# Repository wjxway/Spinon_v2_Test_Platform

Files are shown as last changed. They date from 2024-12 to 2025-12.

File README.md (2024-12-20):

# Maneuverable Piccolissimo 4 (MP4) Test Platform Setup Guide

Maneuverable Piccolissimo 4 test platform, or MP4 test platform for short, is a single motor drone system designed to test the dynamics of the drone before we build the full distributed version of MP4 system. Instead of using peer-to-peer communication between drones to achieve control like it will be in the MP4 system, this test platform uses external optical tracking system like Optitrack to obtain high accuracy drone position, making it easier to test subsystems like aerodynamics or control.

For more details of this system, please check (and cite!) our paper at [RSS proceedings website](https://www.roboticsproceedings.org/rss20/p102.html). For assembly guide, please visit [this document](https://1drv.ms/w/s!Aq5Al0CEiWQnkfE0qJTTQATZVnzniQ).

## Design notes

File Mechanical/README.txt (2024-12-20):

If you want to change the design or look at it in more detail, go to:
https://a360.co/3BthnFp (for the drone)
https://a360.co/49MFVFP (for the launcher)

These parts need to be printed using properly dried PAHT-CF filament using BambuLab X1C printer. (If the filament is just opened, then its dry. If it has been left out for a while, then it needs to be dried. You can use the printer's dry filament utility to dry the filament.)

To print the chassis and the wings, import the process presets in Bambu Studio by Files -> Import -> Import presets. When printing the chassis, select the preset "Chassis" and when printing the wings, select the preset "Wings".

The launcher parts can be printed however you want (PLA+standard settings would work just fine). Just note that Launcher_soft need to be printed using TPU.

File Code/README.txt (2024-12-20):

To use the code, install Platform IO on VSCode, then install the ESP32-Arduino dependencies. For guide, please refer to https://www.youtube.com/watch?v=5edPOlQQKmo.

Before using the code, please change the MAC address specifications in FlightTestOptitrack_Drone, FlightTestOptitrack_Syncer and Launcher_new.
There's a small piece of code there that you can uncomment and then read out the MAC address of the devices through serial port.

If you are using a different tracking system other than Optitrack, you only need to modify FlightTestOptitrack_Server.
If your Optitrack system cannot running at 360Hz, contact me or use FlightTestOptitrack_Server\FIRFilterDesign.m in MATLAB to design a new filter compatible with your setup.

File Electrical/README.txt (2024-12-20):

CAM_Files.zip contains the CAM files needed to manufacture and assemble the PCB.

In the schematics, I'm using pinhead as power plugs and SSM6K504NU FET instead of the G2014.
When building the board, make sure you do not install the pinhead (use wires with headers instead) and install Goford G2014 FET.

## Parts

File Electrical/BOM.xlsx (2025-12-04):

Qty | Value | Device | Package | Parts | Description | ARROW_PART_NUMBER | ARROW_PRICE-STOCK | COPYRIGHT | DESCRIPTION.1 | HEIGHT | MANUFACTURER_NAME | MANUFACTURER_PART_NUMBER | MFR_NAME | MOUSER_PART_NUMBER | MOUSER_PRICE-STOCK | MOUSER_TESTING_PART_NUMBER | MOUSER_TESTING_PRICE-STOCK | POPULARITY | REFDES | SPICEPREFIX | TYPE | Column1
2 |  | PINHD-1X2 | 1X02 | JP2, JP3 | PIN HEADER |  |  |  |  |  |  |  |  |  |  |  |  | 98
2 | 0.1uF | C0402_STANDARD | C0402_STANDARD | C4, C18
2 | 1.5K | R0402_STANDARD | R0402_STANDARD | R7, R20
13 | 10K | R0402_STANDARD | R0402_STANDARD | R4, R16, R17, R18, R22, R24, R25, R26, R27, R28, R29, R42, R43
6 | 10R | R0402_STANDARD | R0402_STANDARD | R10, R11, R12, R13, R14, R15
3 | 10uF | C0402_STANDARD | C0402_STANDARD | C14, C15, C16
1 | 150060RS75000 | 150060RS75000 | LEDC1608X80N | LED1 | WURTH ELEKTRONIK - 150060RS75000 - LED, 0603, RED, 250MCD, 625NM |  |  |  | WURTH ELEKTRONIK - 150060RS75000 - LED, 0603, RED, 250MCD, 625NM | 0.8mm | Wurth Elektronik | 150060RS75000 |  | 710-150060RS75000 | https://www.mouser.co.uk/ProductDetail/Wurth-Elektronik/150060RS75000?qs=LlUlMxKIyB3QnmZ3fw%2FVCA%3D%3D
1 | 15K | R0402_STANDARD | R0402_STANDARD | R3
2 | 1K | R0402_STANDARD | R0402_STANDARD | R19, R23
5 | 2.2uF | C0402_STANDARD | C0402_STANDARD | C10, C11, C12, C13, C31
1 | 2.2uF, 16V | C0402_STANDARD | C0402_STANDARD | C17
1 | 22pF | C0402_STANDARD | C0402_STANDARD | C2
1 | 22uF | C-EUC0603 | C0603 | C3 | CAPACITOR, European symbol |  |  |  |  |  |  |  |  |  |  |  |  | 73 |  | C
1 | 2M | R0402_STANDARD | R0402_STANDARD | R1
1 | 3K | R0402_STANDARD | R0402_STANDARD | R33
3 | 4.7K | R0402_STANDARD | R0402_STANDARD | R30, R31, R32
1 | 4.7uF, 16V | C-EUC0603 | C0603 | C1 | CAPACITOR, European symbol |  |  |  |  |  |  |  |  |  |  |  |  | 73 |  | C
8 | 4.7uF, 16V | C-EUC0805 | C0805 | C19, C20, C22, C23, C24, C25, C26, C27 | CAPACITOR, European symbol |  |  |  |  |  |  |  |  |  |  |  |  | 88 |  | C
2 | 5.1K | R0402_STANDARD | R0402_STANDARD | R5, R6
1 | 5mR | R-EU_R0805 | R0805 | R41 | RESISTOR, European symbol |  |  |  |  |  |  |  |  |  |  |  |  | 86 |  | R
1 | 68K | R0402_STANDARD | R0402_STANDARD | R2
1 | 820R | R0402_STANDARD | R0402_STANDARD | R21
1 | AMCA31-2R450G-S1F-T3 | AMCA31-2R450G-S1F-T3 | ANTC3216X140N | ANT1 | ABRACON - AMCA31-2R450G-S1F-T3 - ANTENNA, CHIP, 2.45GHZ, 50 OHM, 1206 | AMCA31-2R450G-S1F-T3 | https://www.arrow.com/en/products/amca31-2r450g-s1f-t3/abracon?region=nac |  | ABRACON - AMCA31-2R450G-S1F-T3 - ANTENNA, CHIP, 2.45GHZ, 50 OHM, 1206 | 1.4mm | ABRACON | AMCA31-2R450G-S1F-T3 |  | 815-CA312R450GS1FT3 | https://www.mouser.co.uk/ProductDetail/ABRACON/AMCA31-2R450G-S1F-T3?qs=AAveGqk956GLuOddQEK40Q%3D%3D
2 | B3U-1000P | B3U-1000P | B3U-1000P | BOOT, RST | OMRON ELECTRONIC COMPONENTS - B3U-1000P - SWITCH, SPST-NO, 0.05A, 12V, SMD | B3U-1000P | https://www.arrow.com/en/products/b3u1000p/omron?region=europe |  | OMRON ELECTRONIC COMPONENTS - B3U-1000P - SWITCH, SPST-NO, 0.05A, 12V, SMD | mm | Omron Electronics | B3U-1000P |  | 653-B3U-1000P | https://www.mouser.co.uk/ProductDetail/Omron-Electronics/B3U-1000P?qs=AO7BQMcsEu4ip80xyf2FwA%3D%3D
1 | EFM8BB21F16G-C-QFN20R | EFM8BB21F16G-C-QFN20R | EFM8BB21F16GCQFN20R | IC1 | SILICON LABS - EFM8BB21F16G-C-QFN20R - 8 Bit MCU, EFM8 Family EFM8BB Series Microcontrollers, 50 MHz, 16 KB, 2.25 KB, 20 Pins, QFN | EFM8BB21F16G-C-QFN20R | https://www.arrow.com/en/products/efm8bb21f16g-c-qfn20r/silicon-labs?region=nac |  | SILICON LABS - EFM8BB21F16G-C-QFN20R - 8 Bit MCU, EFM8 Family EFM8BB Series Microcontrollers, 50 MHz, 16 KB, 2.25 KB, 20 Pins, QFN | 0.8mm | Silicon Labs | EFM8BB21F16G-C-QFN20R |  | 634-8BB21F16GCQFN20R | https://www.mouser.co.uk/ProductDetail/Silicon-Labs/EFM8BB21F16G-C-QFN20R?qs=6viq6gG%252BWEv0H4U5d9AR5A%3D%3D
1 | ESP32-S3-PICO-1-N8R2 | ESP32-S3-PICO-1-N8R2 | QFN56_7X7_EXP | U2 |  |  |  | Copyright (C) 2024 Ultra Librarian. All rights reserved. |  |  |  | ESP32-S3-PICO-1-N8R2 | Espressif Systems
1 | FD6288Q | FD6288Q | QFN50P400X400X90-25N | IC2 | QFN-24 MOS Drivers RoHS |  |  |  | QFN-24 MOS Drivers RoHS | 0.9mm | Fortior Tech | FD6288Q
1 | GSB1C41110SSHR | GSB1C41110SSHR | GSB1C41110SSHR | J1 | USB2.0, Type C, Top mount, Center Height 1.63mm, Single Row Surface Mount |  |  |  | USB2.0, Type C, Top mount, Center Height 1.63mm, Single Row Surface Mount | 3.41mm | Amphenol Communications Solutions | GSB1C41110SSHR
4 | IN4148WT | IN4148WT | SODFL1608X70N | D1, D2, D3, D4 | SMD Small Signal Switching Diode |  |  |  | SMD Small Signal Switching Diode | 0.7mm | Diotec | IN4148WT
1 | INA231AIYFFR | INA231AIYFFR | BGA12C40P3X4_139X164X62 | IC9 | 28V, Bi-Directional, Low-/High-Side, I2C Out Current/Power Monitor w/Alert in WCSP | INA231AIYFFR | https://www.arrow.com/en/products/ina231aiyffr/texas-instruments?utm_currency=USD&region=nac |  | 28V, Bi-Directional, Low-/High-Side, I2C Out Current/Power Monitor w/Alert in WCSP | 0.625mm | Texas Instruments | INA231AIYFFR |  | 595-INA231AIYFFR | https://www.mouser.co.uk/ProductDetail/Texas-Instruments/INA231AIYFFR?qs=s44pgLhgXQjbCj637LJKHw%3D%3D
1 | SM0605RGB | SM0605RGB | SM0605RGB | LED3 | SM0605RGB, Bivar 470 nm, 525 nm, 635 nm 3 RGB LED, 4-Pin 0605 Clear SMD package | SM0605RGB | https://www.arrow.com/en/products/sm0605rgb/bivar?region=nac |  | SM0605RGB, Bivar 470 nm, 525 nm, 635 nm 3 RGB LED, 4-Pin 0605 Clear SMD package | 0.6mm | Bivar | SM0605RGB |  | 749-SM0605TCRGB | https://www.mouser.co.uk/ProductDetail/Bivar/SM0605RGB?qs=pfd5qewlna4PrJ6da7Zedg%3D%3D
6 | Goford G2014 | Goford G2014 | Goford G2014 | Q6, Q7, Q8, Q9, Q10, Q11 | Small Low ON resistance MOSFETs |  |  |  | Small Low ON resistance MOSFETs | 0.8mm | Toshiba | SSM6K504NU |  | N/A | https://www.mouser.co.uk/ProductDetail/Toshiba/SSM6K504NU?qs=TCEIJQ6oZHxcnwqdmxHSFw%3D%3D
1 | TPSM863252RDXR | TPSM863252RDXR | RDX0007A-MFG | U1 |  |  |  | Copyright (C) 2024 Ultra Librarian. All rights reserved. |  |  |  | TPSM863252RDXR | Texas Instruments |  |  |  |  |  | RefDes |  | TYPE

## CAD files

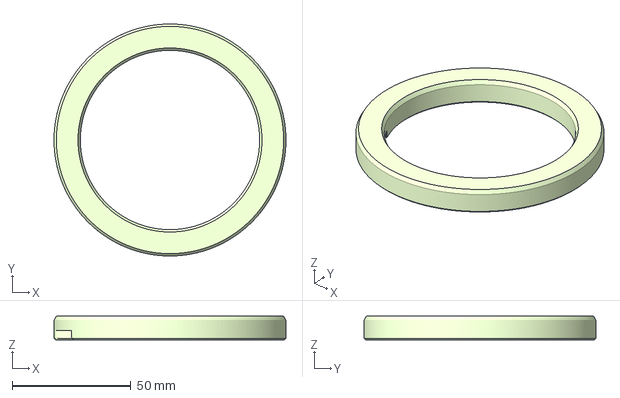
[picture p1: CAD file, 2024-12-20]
Mechanical/Launcher_soft.3mf
97.6 x 97.6 x 10.0 mm

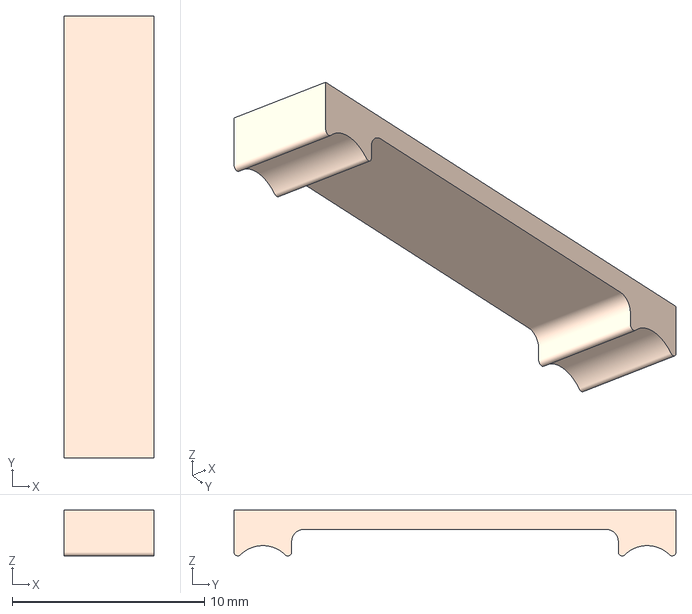
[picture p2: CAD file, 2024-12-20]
Mechanical/Launcher_cap_1.3mf
4.70 x 23.0 x 2.38 mm

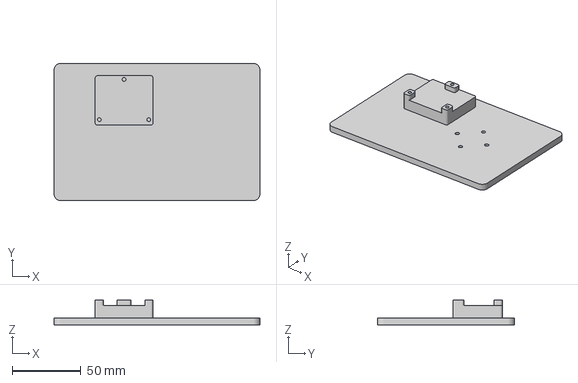
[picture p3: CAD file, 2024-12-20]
Mechanical/Launcher_base.3mf
150.0 x 100.0 x 18.1 mm

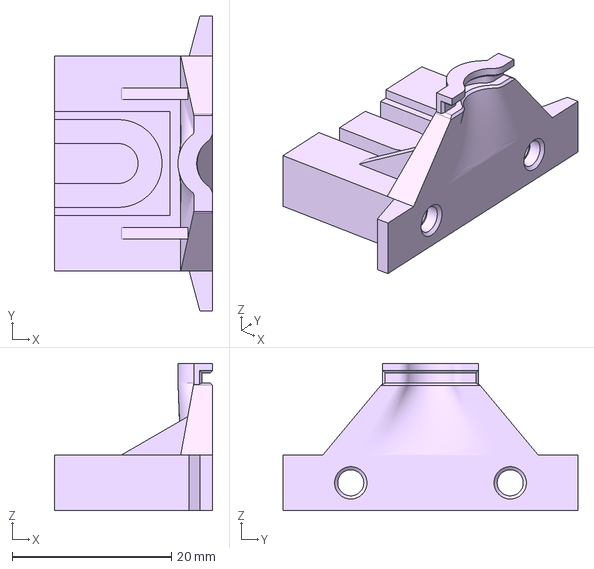
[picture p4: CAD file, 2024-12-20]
Mechanical/Launcher_slider.3mf
19.9 x 37.0 x 18.5 mm

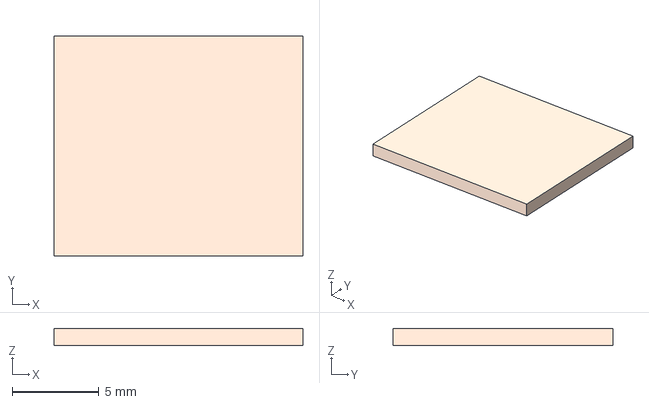
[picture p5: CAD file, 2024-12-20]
Mechanical/Launcher_cap_2.3mf
14.3 x 12.7 x 1.00 mm

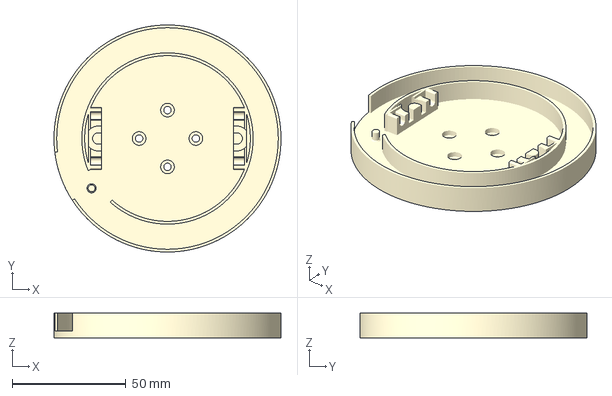
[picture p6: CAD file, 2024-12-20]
Mechanical/Launcher_platform.3mf
100.0 x 100.0 x 11.0 mm

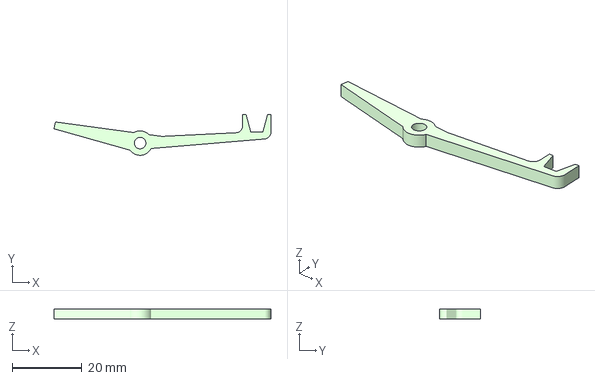
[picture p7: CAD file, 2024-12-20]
Mechanical/Launcher_lever.3mf
62.2 x 11.6 x 3.00 mm

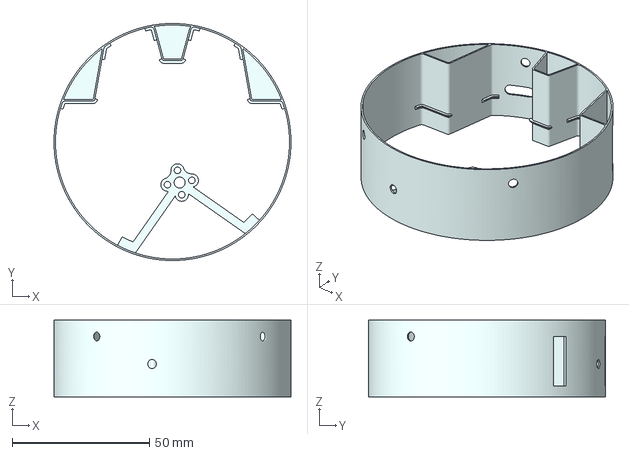
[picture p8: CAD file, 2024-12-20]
Mechanical/Chassis.3mf
86.3 x 86.3 x 28.0 mm

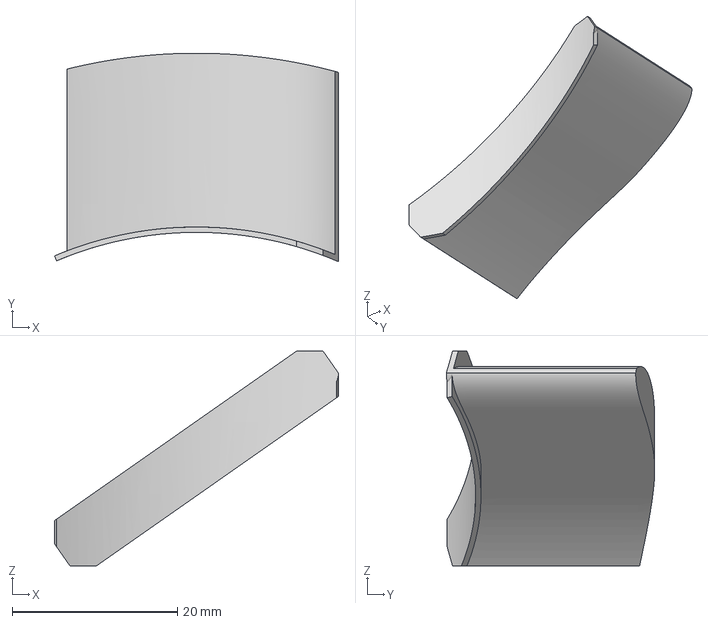
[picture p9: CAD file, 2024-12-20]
Mechanical/Wings.3mf
34.4 x 25.2 x 26.0 mm

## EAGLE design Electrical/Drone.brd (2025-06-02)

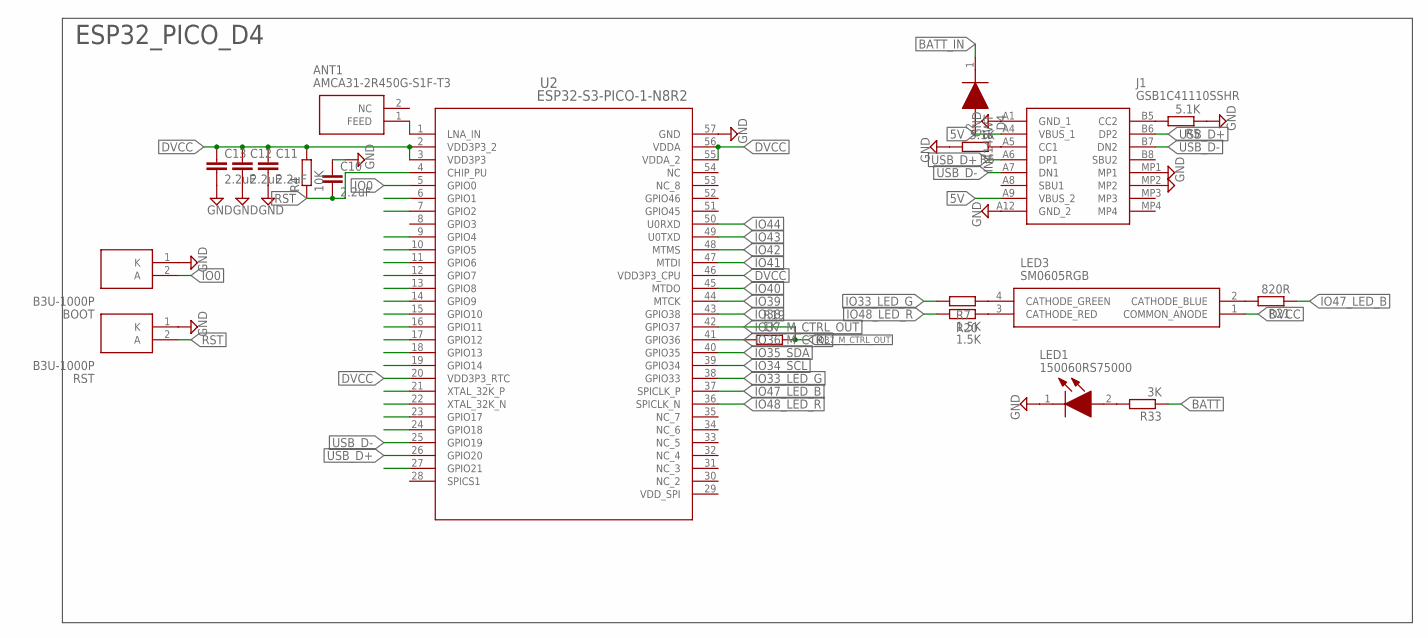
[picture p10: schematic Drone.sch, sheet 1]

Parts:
ANT1: AMCA31-2R450G-S1F-T3; ANTC3216X140N
BOOT: B3U-1000P
C10, C11, C12, C13: 2.2uF; C0402_STANDARD
D4: IN4148WT; SODFL1608X70N
J1: GSB1C41110SSHR
LED1: 150060RS75000; LEDC1608X80N
LED3: SM0605RGB
R4: 10K; R0402_STANDARD
R5, R6: 5.1K; R0402_STANDARD
R7, R20: 1.5K; R0402_STANDARD
R19: 1K; R0402_STANDARD
R21: 820R; R0402_STANDARD
R33: 3K; R0402_STANDARD
RST: B3U-1000P
U2: ESP32-S3-PICO-1-N8R2; QFN56_7X7_EXP

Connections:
5V: D4.2 (A), J1.A4 (VBUS_1), J1.A9 (VBUS_2)
BATT: R33.1; also elsewhere on the board
BATT_IN: D4.1 (K); also elsewhere on the board
DVCC: C11.1, C12.1, C13.1, LED3.1 (COMMON_ANODE), R4.2, U2.2 (VDD3P3_2), U2.3 (VDD3P3), U2.20 (VDD3P3_RTC), U2.46 (VDD3P3_CPU), U2.55 (VDDA_2), U2.56 (VDDA); also elsewhere on the board
GND: BOOT.1 (K), C10.1, C11.2, C12.2, C13.2, J1.A1 (GND_1), J1.A12 (GND_2), J1.MP1, J1.MP2, LED1.1 (K), R5.1, R6.2, RST.1 (K), U2.57 (GND); also elsewhere on the board
IO0: BOOT.2 (A), U2.5 (GPIO0)
IO33_LED_G: R7.2, U2.38 (GPIO33)
IO34_SCL: U2.39 (GPIO34); also elsewhere on the board
IO35_SDA: U2.40 (GPIO35); also elsewhere on the board
IO36_M_CTRL: R19.2, U2.41 (GPIO36)
IO37_M_CTRL_OUT: R19.1, U2.42 (GPIO37); also elsewhere on the board
IO38: U2.43 (GPIO38)
IO39: U2.44 (MTCK)
IO40: U2.45 (MTDO)
IO41: U2.47 (MTDI)
IO42: U2.48 (MTMS)
IO43: U2.49 (U0TXD)
IO44: U2.50 (U0RXD)
IO47_LED_B: R21.1, U2.37 (SPICLK_P)
IO48_LED_R: R20.2, U2.36 (SPICLK_N)
unnamed: ANT1.1 (FEED), U2.1 (LNA_IN)
unnamed: LED3.4 (CATHODE_GREEN), R7.1
unnamed: J1.A5 (CC1), R6.1
unnamed: LED1.2 (A), R33.2
unnamed: LED3.2 (CATHODE_BLUE), R21.2
unnamed: J1.B5 (CC2), R5.2
unnamed: LED3.3 (CATHODE_RED), R20.1
RST: C10.2, R4.1, RST.2 (A), U2.4 (CHIP_PU)
USB_D+: J1.A6 (DP1), J1.B6 (DP2), U2.26 (GPIO20)
USB_D-: J1.A7 (DN1), J1.B7 (DN2), U2.25 (GPIO19)
VDD_SPI: U2.29 (VDD_SPI)

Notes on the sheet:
ESP32_PICO_D4

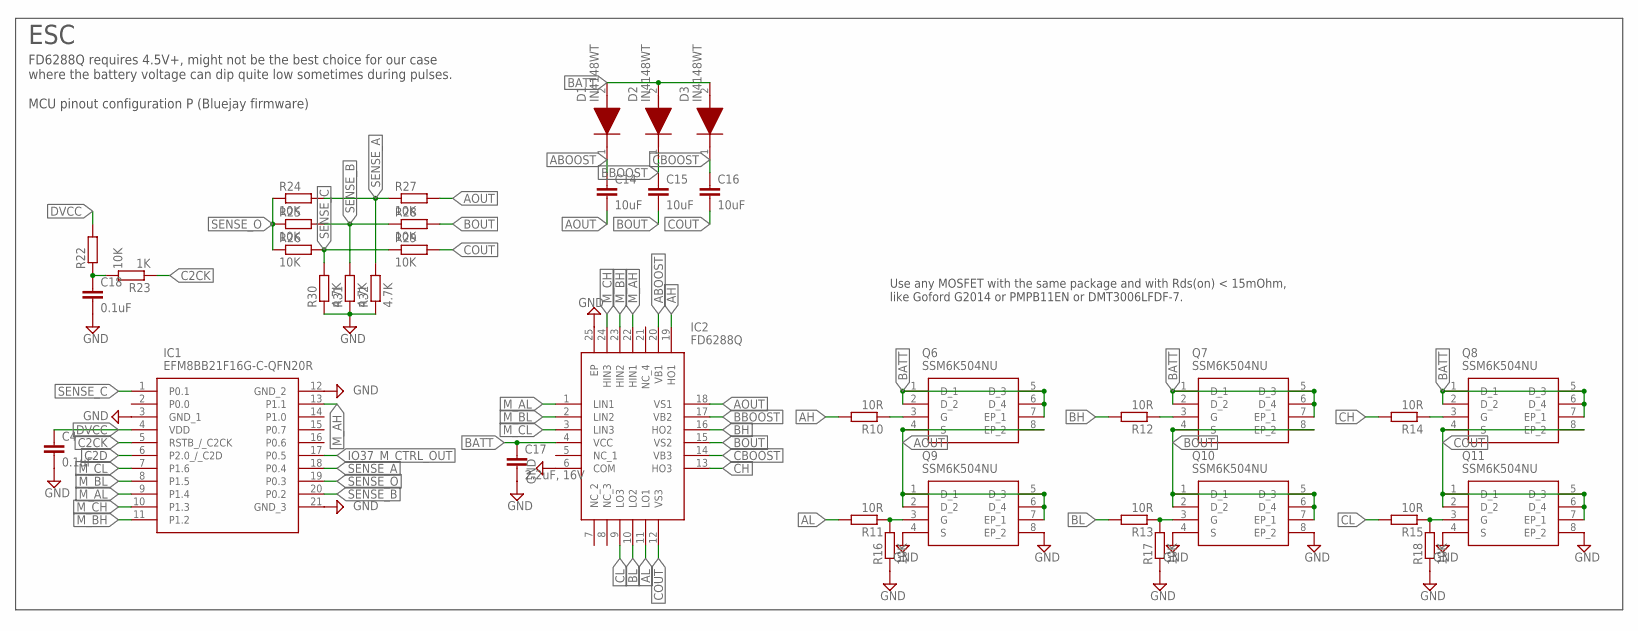
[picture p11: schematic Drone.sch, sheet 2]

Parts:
C4, C18: 0.1uF; C0402_STANDARD
C14, C15, C16: 10uF; C0402_STANDARD
C17: 2.2uF, 16V; C0402_STANDARD
D1, D2, D3: IN4148WT; SODFL1608X70N
IC1: EFM8BB21F16G-C-QFN20R; EFM8BB21F16GCQFN20R
IC2: FD6288Q; QFN50P400X400X90-25N
Q6, Q7, Q8, Q9, Q10, Q11: SSM6K504NU
R10, R11, R12, R13, R14, R15: 10R; R0402_STANDARD
R16, R17, R18, R22, R24, R25, R26, R27, R28, R29: 10K; R0402_STANDARD
R23: 1K; R0402_STANDARD
R30, R31, R32: 4.7K; R0402_STANDARD

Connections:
ABOOST: C14.1, D1.1 (K), IC2.20 (VB1)
AH: IC2.19 (HO1), R10.2
AL: IC2.11 (LO1), R11.2
AOUT: C14.2, IC2.18 (VS1), Q6.4 (S), Q6.8 (EP_2), Q9.1 (D_1), Q9.2 (D_2), Q9.5 (D_3), Q9.6 (D_4), Q9.7 (EP_1), R27.2
BATT: C17.1, D1.2 (A), D2.2 (A), D3.2 (A), IC2.4 (VCC), Q6.1 (D_1), Q6.2 (D_2), Q6.5 (D_3), Q6.6 (D_4), Q6.7 (EP_1), Q7.1 (D_1), Q7.2 (D_2), Q7.5 (D_3), Q7.6 (D_4), Q7.7 (EP_1), Q8.1 (D_1), Q8.2 (D_2), Q8.5 (D_3), Q8.6 (D_4), Q8.7 (EP_1); also elsewhere on the board
BBOOST: C15.1, D2.1 (K), IC2.17 (VB2)
BH: IC2.16 (HO2), R12.2
BL: IC2.10 (LO2), R13.2
BOUT: C15.2, IC2.15 (VS2), Q7.4 (S), Q7.8 (EP_2), Q10.1 (D_1), Q10.2 (D_2), Q10.5 (D_3), Q10.6 (D_4), Q10.7 (EP_1), R28.2
C2CK: IC1.5 (RSTB_/_C2CK), R23.1
C2D: IC1.6 (P2.0_/_C2D)
CBOOST: C16.1, D3.1 (K), IC2.14 (VB3)
CH: IC2.13 (HO3), R14.2
CL: IC2.9 (LO3), R15.2
COUT: C16.2, IC2.12 (VS3), Q8.4 (S), Q8.8 (EP_2), Q11.1 (D_1), Q11.2 (D_2), Q11.5 (D_3), Q11.6 (D_4), Q11.7 (EP_1), R29.2
DVCC: C4.1, IC1.4 (VDD), R22.2; also elsewhere on the board
GND: C4.2, C17.2, C18.2, IC1.3 (GND_1), IC1.12 (GND_2), IC1.21 (GND_3), IC2.6 (COM), IC2.25 (EP), Q9.4 (S), Q9.8 (EP_2), Q10.4 (S), Q10.8 (EP_2), Q11.4 (S), Q11.8 (EP_2), R16.1, R17.1, R18.1, R30.1, R31.1, R32.1; also elsewhere on the board
IO37_M_CTRL_OUT: IC1.17 (P0.5); also elsewhere on the board
M_AH: IC1.13 (P1.1), IC2.22 (HIN1)
M_AL: IC1.9 (P1.4), IC2.1 (LIN1)
M_BH: IC1.11 (P1.2), IC2.23 (HIN2)
M_BL: IC1.8 (P1.5), IC2.2 (LIN2)
M_CH: IC1.10 (P1.3), IC2.24 (HIN3)
M_CL: IC1.7 (P1.6), IC2.3 (LIN3)
unnamed: Q6.3 (G), R10.1
unnamed: Q9.3 (G), R11.1, R16.2
unnamed: Q7.3 (G), R12.1
unnamed: Q10.3 (G), R13.1, R17.2
unnamed: Q8.3 (G), R14.1
unnamed: Q11.3 (G), R15.1, R18.2
unnamed: C18.1, R22.1, R23.2
SENSE_A: IC1.18 (P0.4), R24.2, R27.1, R32.2
SENSE_B: IC1.20 (P0.2), R25.2, R28.1, R31.2
SENSE_C: IC1.1 (P0.1), R26.2, R29.1, R30.2
SENSE_O: IC1.19 (P0.3), R24.1, R25.1, R26.1

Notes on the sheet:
ESC
FD6288Q requires 4.5V+, might not be the best choice for our case where the battery voltage can dip quite low sometimes during pulses. MCU pinout configuration P (Bluejay firmware)
Use any MOSFET with the same package and with Rds(on) < 15mOhm, like Goford G2014 or PMPB11EN or DMT3006LFDF-7.

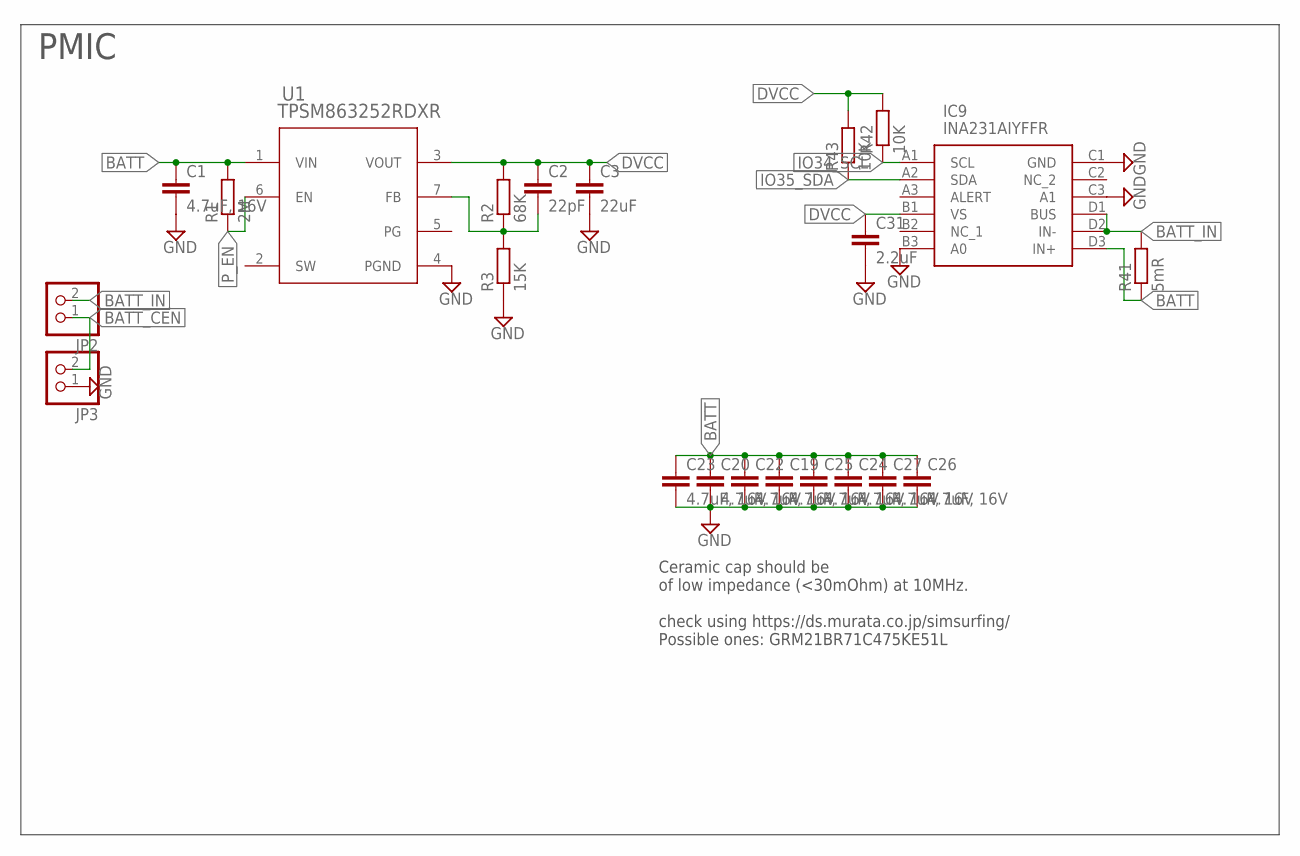
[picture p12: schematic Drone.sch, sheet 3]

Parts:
C1: 4.7uF, 16V; C0603
C2: 22pF; C0402_STANDARD
C3: 22uF; C0603
C19, C20, C22, C23, C24, C25, C26, C27: 4.7uF, 16V; C0805
C31: 2.2uF; C0402_STANDARD
IC9: INA231AIYFFR; BGA12C40P3X4_139X164X62
JP2, JP3: PINHD-1X2; 1X02
R1: 2M; R0402_STANDARD
R2: 68K; R0402_STANDARD
R3: 15K; R0402_STANDARD
R41: 5mR; R0805
R42, R43: 10K; R0402_STANDARD
U1: TPSM863252RDXR; RDX0007A-MFG

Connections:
BATT: C1.1, C19.1, C20.1, C22.1, C23.1, C24.1, C25.1, C26.1, C27.1, IC9.D3 (IN+), R1.2, R41.1, U1.1 (VIN); also elsewhere on the board
BATT_CEN: JP2.1, JP3.2
BATT_IN: IC9.D1 (BUS), IC9.D2 (IN-), JP2.2, R41.2; also elsewhere on the board
DVCC: C2.1, C3.1, C31.1, IC9.B1 (VS), R2.2, R42.2, R43.2, U1.3 (VOUT); also elsewhere on the board
GND: C1.2, C3.2, C19.2, C20.2, C22.2, C23.2, C24.2, C25.2, C26.2, C27.2, C31.2, IC9.B3 (A0), IC9.C1 (GND), IC9.C3 (A1), JP3.1, R3.1, U1.4 (PGND); also elsewhere on the board
IO34_SCL: IC9.A1 (SCL), R42.1; also elsewhere on the board
IO35_SDA: IC9.A2 (SDA), R43.1; also elsewhere on the board
unnamed: C2.2, R2.1, R3.2, U1.7 (FB)
P_EN: R1.1, U1.6 (EN)

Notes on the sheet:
PMIC
Ceramic cap should be of low impedance (<30mOhm) at 10MHz. check using https://ds.murata.co.jp/simsurfing/ Possible ones: GRM21BR71C475KE51L

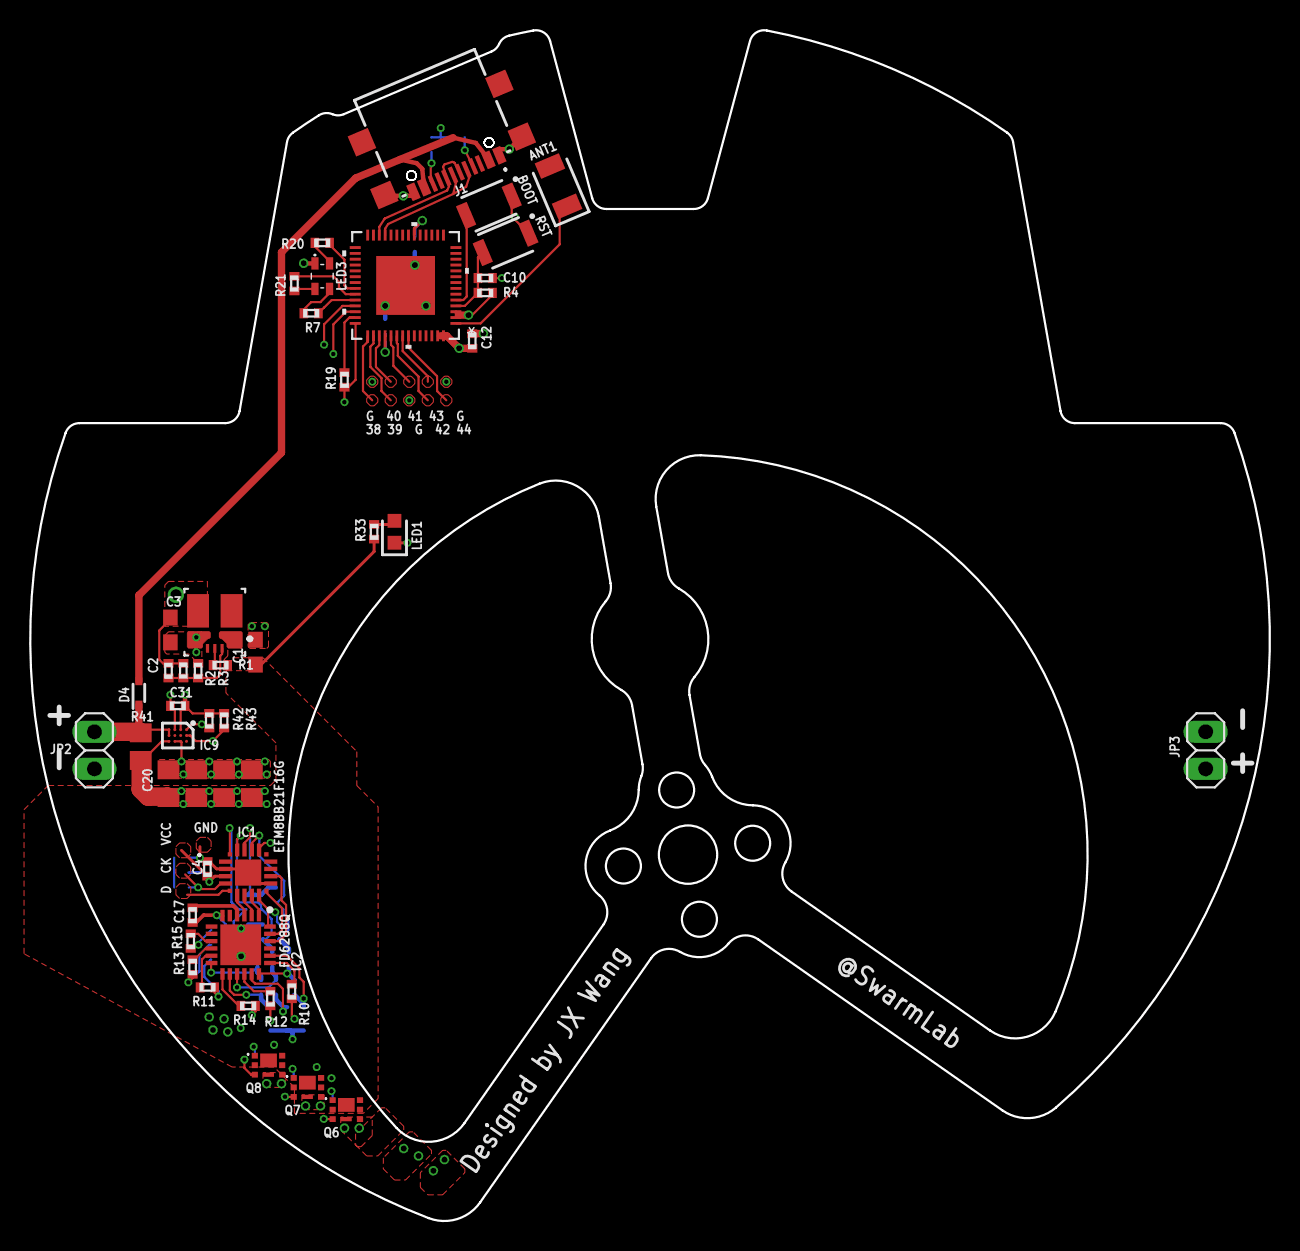
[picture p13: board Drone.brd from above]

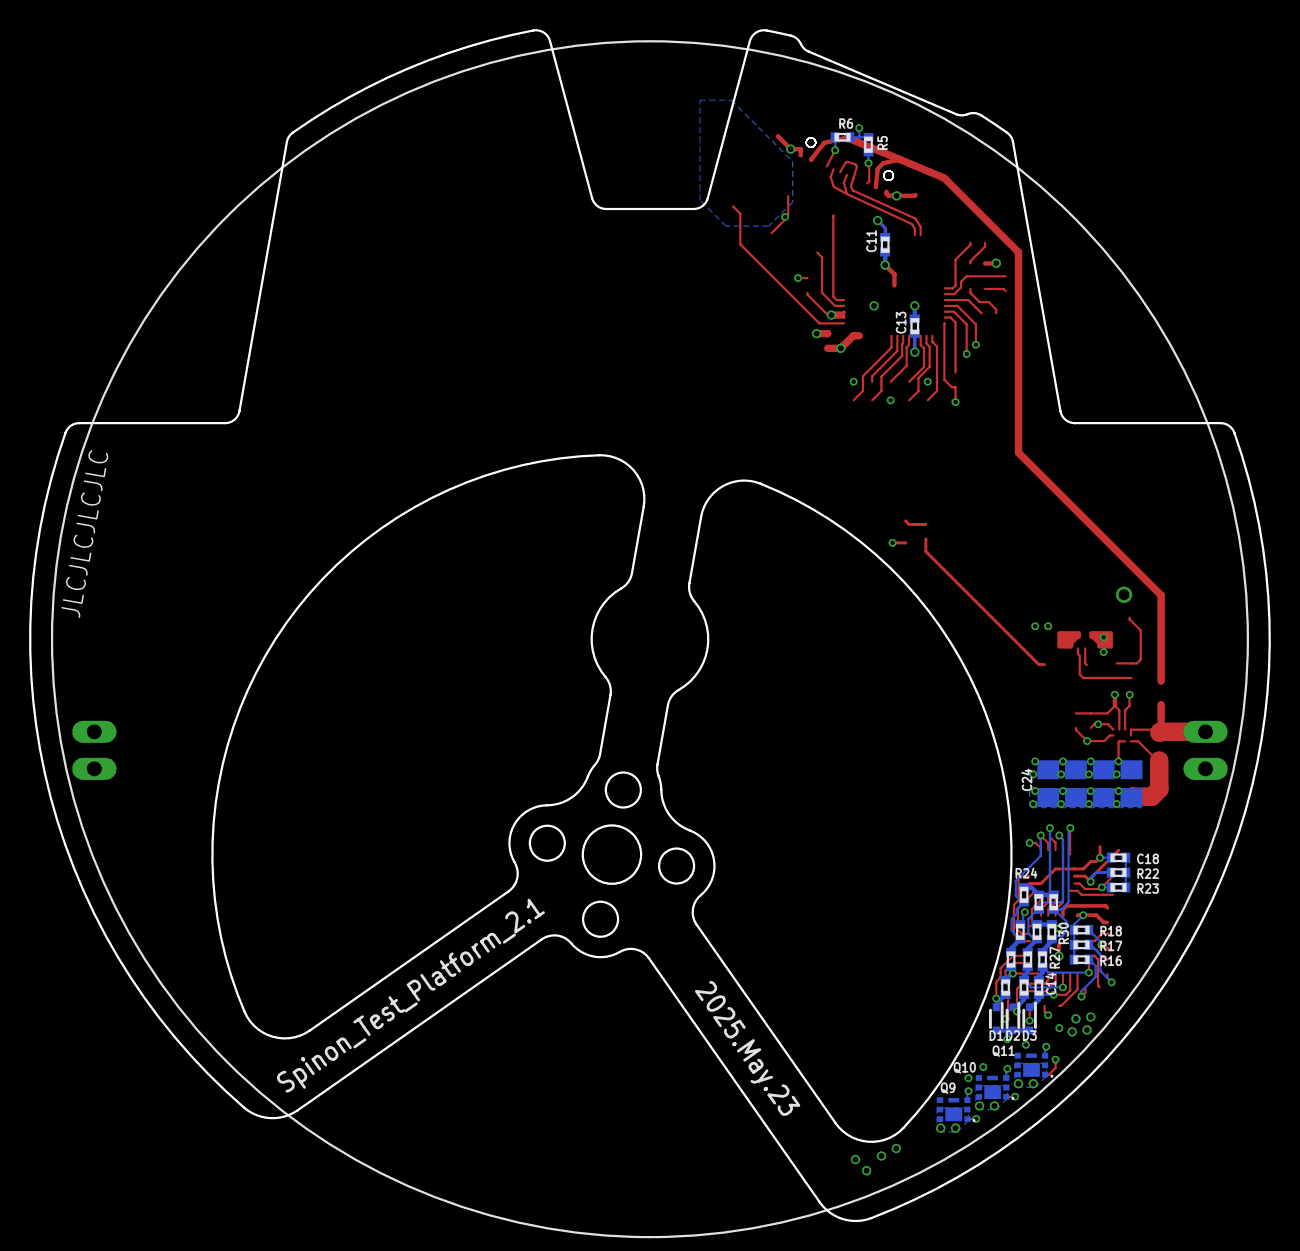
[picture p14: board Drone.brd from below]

Board: 4 copper layers, 85.0 x 81.6 mm, 79 parts (32 on the bottom side), 56 nets.

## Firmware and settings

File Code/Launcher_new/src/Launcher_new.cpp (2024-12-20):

#include "Arduino.h"
#include <MotorCtrl.hpp>
#include <TimeSync.hpp>
#include <ESPNOWCOMM.hpp>

using std::array;

#define SERVO_LEDC_CHANNEL 0
#define SERVO_PIN 12

#define MOTOR_TX_PIN 15
#define MOTOR_RX_PIN 13

#define LED_PIN 9

// servo values
constexpr uint32_t no_trig_val = 457;
constexpr uint32_t trig_val = 435;
constexpr uint32_t full_val = 300;

// ESP-NOW settings
array<uint8_t, 6> station_MAC = {0xF4, 0x12, 0xFA, 0x88, 0x13, 0xD0}; // This is for ESP32-S3 dev board
array<uint8_t, 6> launcher_mac = {0x64, 0xB7, 0x08, 0x9D, 0x69, 0xCC};

constexpr int WiFi_channel = 14;

// global shared variable to indicate whether the launch is intialized or canceled
bool launch_inited = false;
bool launch_canceled = false;
// synced launch time
int64_t synced_launch_time = 0;

// terminal velocity in 0.01dps/LSB (might be slightly inaccurate)
int32_t velocity = 720000;

/**
 * @brief launch the drone task
 */
void Launch(void *pvParameters)
{
    // prevent launching too frequently
    static int64_t last_local_launch_time = 0;
    constexpr int64_t min_launch_time_gap = 10000000;
    if (esp_timer_get_time() - last_local_launch_time < min_launch_time_gap)
    {
        launch_inited = false;
        vTaskDelete(NULL);
    }

    Motor::Resume();
    Motor::Set_velocity(velocity);

    // cancel launch if signaled
    for (int i = 0; i < 40; i++)
    {
        vTaskDelay(pdMS_TO_TICKS(100));
        if (launch_canceled)
        {
            Motor::Set_velocity(0);
            Motor::Stop();
            launch_inited = false;
            vTaskDelete(NULL);
        }
    }

    while (true)
    {
        // get current angle in degrees
        Motor::Read_motor_state();
        float pos = float(Motor::motor_position) / 65536.0F * 360.0F;
        if (345.0F > pos && pos > 335.0F)
        {
            synced_launch_time = TimeSync::Get_synced_time();
            last_local_launch_time = esp_timer_get_time();
            break;
        }
    }

    // trigger servo to launch the drone
    ledcWrite(SERVO_LEDC_CHANNEL, full_val);
    delay(25);

    ledcWrite(SERVO_LEDC_CHANNEL, trig_val);
    delay(100);

    ledcWrite(SERVO_LEDC_CHANNEL, no_trig_val);

    // stop motor after launch
    Motor::Set_velocity(0);
    Motor::Stop();

    launch_inited = false;
    vTaskDelete(NULL);
}

void Trigger_Launch_Task(void *pvParameters)
{
    auto data_queue = TimeSync::Get_data_queue_handle();

    while (true)
    {
        // receive data
        uint8_t temp_data[TimeSync::max_data_len] = {0};
        xQueueReceive(data_queue, temp_data, portMAX_DELAY);
        uint8_t temp_data_len = temp_data[0];

        if (temp_data_len == 4 && TimeSync::SyncedQ() && !launch_inited)
        {
            velocity=*(int32_t*)(temp_data+1);
            launch_canceled = false;
            launch_inited = true;
            xTaskCreate(Launch, "Launch", 10000, nullptr, 10, NULL);
        }
        // cancel the launch if 23 is received
        else if (temp_data_len == 1 && temp_data[1] == 23 && launch_inited)
        {
            launch_inited = false;
            launch_canceled = true;
        }
    }
}

void setup()
{
    Serial.begin(115200);
    Serial.println("Program Start!");

    pinMode(LED_PIN, OUTPUT);
    digitalWrite(LED_PIN, LOW);

    // servo init and test
    ledcSetup(SERVO_LEDC_CHANNEL, 300, 10);
    ledcAttachPin(SERVO_PIN, SERVO_LEDC_CHANNEL);

    ledcWrite(SERVO_LEDC_CHANNEL, no_trig_val);
    delay(500);
    ledcWrite(SERVO_LEDC_CHANNEL, trig_val);
    delay(500);
    ledcWrite(SERVO_LEDC_CHANNEL, no_trig_val);
    delay(500);

    // init motor
    Motor::Init(MOTOR_TX_PIN, MOTOR_RX_PIN);
    Motor::Resume();
    Motor::Set_PID(30, 30, 10, 6, 40, 30);

    Motor::Set_incremental_position_2(2000, 6000);
    delay(500);
    Motor::Set_incremental_position_2(-2000, 6000);
    delay(500);
    Motor::Stop();

    // initialize ESP-NOW
    if (ESPNOWCOMM::Init(WiFi_channel) != 0)
    {
        Serial.println("ESP NOW init failure!");
    }

    // register peers
    ESPNOWCOMM::Register_peer(station_MAC);

    TimeSync::Init();
    ESPNOWCOMM::Set_receive_callback(TimeSync::Receive_Callback);

    xTaskCreatePinnedToCore(Trigger_Launch_Task, "Trigger_Launch_Task", 10000, nullptr, 11, NULL, 0);

    Serial.println("Init End!");
}

void loop()
{
    vTaskDelay(pdMS_TO_TICKS(200));
    if (TimeSync::SyncedQ())
    {
        digitalWrite(LED_PIN, HIGH);
    }
    else
    {
        digitalWrite(LED_PIN, LOW);
    }

    // send, send and send
    if (synced_launch_time != -1 && synced_launch_time != 0)
    {
        // send once here, send many more later...
        // convert launch time to byte array and send
        uint8_t synced_launch_time_bytes[8];
        memcpy(synced_launch_time_bytes, &synced_launch_time, 8);
        ESPNOWCOMM::Send(0, synced_launch_time_bytes, 8);
    }
}

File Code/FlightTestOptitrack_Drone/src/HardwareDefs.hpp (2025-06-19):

/**
 * @file HardwareDefs.hpp
 * @brief Hardware pin definitions and resource configurations.
 */

#ifndef HARDWARE_DEFS_HPP
#define HARDWARE_DEFS_HPP

#include "Arduino.h"
#include <array>

// LED pin definitions
#define LED_R 48
#define LED_G 33
#define LED_B 47

// motor input and output
#define M_CTRL_OUT 36
#define M_CTRL_IN 37

// power management
#define PWR_SCL 34
#define PWR_SDA 35

// ESP-NOW settings
std::array<uint8_t, 6> station_MAC = {0xF4, 0x12, 0xFA, 0x88, 0x13, 0xD0};
// array<uint8_t, 6> spinon_MAC = {0x64, 0xE8, 0x33, 0x72, 0x02, 0x94}; // Spinon 21
std::array<uint8_t, 6> spinon_MAC = {0x64, 0xE8, 0x33, 0x72, 0x02, 0xF4}; // Spinon 22
constexpr int WiFi_channel = 14;

// Power monitoring setup
const uint32_t SHUNT_MICRO_OHM = 5000;  // Shunt resistance in Micro-Ohm, 5000 = 5 mOhm
const uint16_t MAXIMUM_AMPS = 10;       // Max expected amps for drone application

#endif

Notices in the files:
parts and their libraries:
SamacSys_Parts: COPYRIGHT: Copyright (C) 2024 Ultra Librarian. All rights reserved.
